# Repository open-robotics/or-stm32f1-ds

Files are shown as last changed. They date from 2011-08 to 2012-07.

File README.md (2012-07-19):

OR-STM32F1-DS
=============

Open Robotics controller based on STM32F103VC chip.

Feauters
--------

* 20 servo control outputs
* 8 RoboGPIO with ADC option
* 8 RoboGPIO with servo option
* Onboard dual channel motor H-dirver
* RoboMD2 for additional external motor driver
* Onboard USB
* Separated I<sup>2</sup>C in RoboBUS and RoboI2C
* 2 quadrature encoder inputs

Connectors
----------

* 20 Servo
* 16 RoboGPIO
* 2 brush motor
* 1 RoboBUS
* 1 RoboMD2
* 1 RoboI2C
* 1 USB

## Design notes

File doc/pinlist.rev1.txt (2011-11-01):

Pinlist

Exported from or-stm32-ds.sch at 01.11.11 23:47

EAGLE Version 5.11.0 Copyright (c) 1988-2010 CadSoft

Part     Pad      Pin        Dir      Net

C1       +        +          Pas      VMD
         -        -          Pas      GND

C2       +        +          Pas      VMD
         -        -          Pas      GND

C3       +        +          Pas      VREG5
         -        -          Pas      GND

C4       +        +          Pas      VREG33
         -        -          Pas      GND

C5       1        1          Pas      GND
         2        2          Pas      N$2

C6       1        1          Pas      GND
         2        2          Pas      N$3

C7       1        1          Pas      +3V3
         2        2          Pas      GND

C8       1        1          Pas      +3V3
         2        2          Pas      GND

C9       1        1          Pas      +3V3
         2        2          Pas      GND

C10      1        1          Pas      +3V3
         2        2          Pas      GND

C11      1        1          Pas      +3V3
         2        2          Pas      GND

C12      1        1          Pas      !NRST
         2        2          Pas      GND

C13      1        1          Pas      VREG33
         2        2          Pas      GND

C14      1        1          Pas      VREG5
         2        2          Pas      GND

DA1      1        GND        In       GND
         2        OUT        Pas      VREG5
         3        IN         In       VS1

DA2      1        GND        In       GND
         2        OUT        Pas      VREG33
         3        IN         In       VS1

DD1      1        PE2        I/O      S04
         2        PE3        I/O      S03
         3        PE4        I/O      S02
         4        PE5        I/O      S01
         5        PE6        I/O      S00
         6        VBAT       I/O               *** unconnected ***
         7        PC13-TAMPER-RTC I/O               *** unconnected ***
         8        PC14-OSC32_IN I/O               *** unconnected ***
         9        PC15-OSC32_OUT I/O               *** unconnected ***
         10       VSS_5      Pas      GND
         11       VDD_5      Pwr      +3V3
         12       OSC_IN     In       N$2
         13       OSC_OUT    Out      N$3
         14       !NRST      In       !NRST
         15       PC0        I/O      AG7
         16       PC1        I/O      AG6
         17       PC2        I/O      AG5
         18       PC3        I/O      AG4
         19       VSSA       I/O      GND
         20       VREF-      I/O      GND
         21       VREF+      I/O      +3V3
         22       VDDA       I/O      +3V3
         23       PA0-WKUP   I/O      AG3
         24       PA1        I/O      AG2
         25       PA2        I/O      AG1
         26       PA3        I/O      AG0
         27       VSS_4      Pas      GND
         28       VDD_4      Pwr      +3V3
         29       PA4        I/O      DAC1
         30       PA5        I/O      DAC2
         31       PA6        I/O      E0F0
         32       PA7        I/O      E0F1
         33       PC4        I/O      M0DIRP
         34       PC5        I/O      M0DIRN
         35       PB0        I/O      M1DIRP
         36       PB1        I/O      M1DIRN
         37       PB2-BOOT1  I/O      BOOT1
         38       PE7        I/O      MDDIR1
         39       PE8        I/O      M0PWMN
         40       PE9        I/O      M0PWMP
         41       PE10       I/O      M1PWMN
         42       PE11       I/O      M1PWMP
         43       PE12       I/O      MDDIR2
         44       PE13       I/O      MDPWM1
         45       PE14       I/O      MDPWM2
         46       PE15       I/O               *** unconnected ***
         47       PB10       I/O      I2C-SCL/TX
         48       PB11       I/O      I2C-SDA/RX
         49       VSS_1      Pas      GND
         50       VDD_1      Pwr      +3V3
         51       PB12       I/O      G0
         52       PB13       I/O      G1
         53       PB14       I/O      G2
         54       PB15       I/O      G3
         55       PD8        I/O      G4
         56       PD9        I/O      G5
         57       PD10       I/O      G6
         58       PD11       I/O      G7
         59       PD12       I/O      E1F0
         60       PD13       I/O      E1F1
         61       PD14       I/O      S10
         62       PD15       I/O      S11
         63       PC6        I/O      S12
         64       PC7        I/O      S13
         65       PC8        I/O      S14
         66       PC9        I/O      S15
         67       PA8        I/O      S16
         68       PA9        I/O      U2TX
         69       PA10       I/O      U2RX
         70       PA11       I/O      USBD-
         71       PA12       I/O      USBD+
         72       PA13       I/O      SWDIO
         73       NC         NC                *** unconnected ***
         74       VSS_2      Pas      GND
         75       VDD_2      Pwr      +3V3
         76       PA14       I/O      SWCLK
         77       PA15       I/O      RBGP0
         78       PC10       I/O      S17
         79       PC11       I/O      S18
         80       PC12       I/O      S19
         81       PD0        I/O      RBGP1
         82       PD1        I/O      RBGP2
         83       PD2        I/O      RBGP0
         84       PD3        I/O               *** unconnected ***
         85       PD4        I/O               *** unconnected ***
         86       PD5        I/O      S09
         87       PD6        I/O      S08
         88       PD7        I/O      S07
         89       PB3        I/O      RBSCK
         90       PB4        I/O      RBMISO
         91       PB5        I/O      RBMOSI
         92       PB6        I/O      RBSCL
         93       PB7        I/O      RBSDA
         94       BOOT0      In       BOOT0
         95       PB8        I/O      CAN_RX
         96       PB9        I/O      CAN_TX
         97       PE0        I/O      S06
         98       PE1        I/O      S05
         99       VSS_3      Pas      GND
         100      VDD_3      Pwr      +3V3

DD2      1        TXD        In       CAN_TX
         2        VSS        Pwr      GND
         3        VDD        Pwr      +3V3
         4        RXD        Out      CAN_RX
         5        VREF       Pwr      VREF
         6        CANL       I/O      CANL
         7        CANH       I/O      CANH
         8        RS         In       CANRS

HL1      A        A          Pas      +3V3
         C        C          Pas      N$6

HL2      A        A          Pas      N$7
         C        C          Pas      GND

HL3      1        C          Pas      N$10
         2        A          Pas      M0C-
         3        C          Pas      M0C-
         4        A          Pas      N$10

HL4      1        C          Pas      N$13
         2        A          Pas      M0C-1
         3        C          Pas      M0C-1
         4        A          Pas      N$13

JP3      1        1          Pas      VREG5
         2        2          Pas      +5V

JP4      1        1          Pas      VREG33
         2        2          Pas      +3V3

JP5      1        1          Pas      U2RX
         2        2          Pas      N$5
         3        3          Pas      N$1
         4        4          Pas      U2TX

JP6      1        1          Pas      +3V3
         2        2          Pas      GPVCC
         3        3          Pas      VS1

JP7      1        1          Pas      +3V3
         2        2          Pas      N$4
         3        3          Pas      VS0

R1       1        1          Pas      GND
         2        2          Pas      N$6

R2       1        1          Pas      +3V3
         2        2          Pas      RBSDA

R3       1        1          Pas      +3V3
         2        2          Pas      RBSCL

R4       1        1          Pas      GND
         2        2          Pas      BOOT1

R5       1        1          Pas      M0DIRP
         2        2          Pas      GND

R6       1        1          Pas      N$7
         2        2          Pas      BOOT1

R7       1        1          Pas      GND
         2        2          Pas      M0PWMP

R8       1        1          Pas      N$8
         2        2          Pas      VMD

R9       1        1          Pas      M0C+
         2        2          Pas      N$10

R10      1        1          Pas      VMD
         2        2          Pas      N$9

R11      1        1          Pas      GND
         2        2          Pas      M0PWMN

R12      1        1          Pas      M0DIRN
         2        2          Pas      GND

R13      1        1          Pas      M1DIRP
         2        2          Pas      GND

R14      1        1          Pas      GND
         2        2          Pas      M1PWMP

R15      1        1          Pas      N$11
         2        2          Pas      VMD

R16      1        1          Pas      BOOT0
         2        2          Pas      GND

R17      1        1          Pas      M0C+1
         2        2          Pas      N$13

R18      1        1          Pas      VMD
         2        2          Pas      N$12

R19      1        1          Pas      GND
         2        2          Pas      M1PWMN

R20      1        1          Pas      I2C-SDA/RX
         2        2          Pas      +5V

R21      1        1          Pas      I2C-SCL/TX
         2        2          Pas      +5V

R22      1        1          Pas      M1DIRN
         2        2          Pas      GND

R23      1        1          Pas      USBD+
         2        2          Pas      +3V3

R24      1        1          Pas      GND
         2        2          Pas      CANRS

R25      1        1          Pas      +5V
         2        2          Pas      S00C

R26      1        1          Pas      +5V
         2        2          Pas      S01C

R27      1        1          Pas      +5V
         2        2          Pas      S02C

R28      1        1          Pas      +5V
         2        2          Pas      S03C

R29      1        1          Pas      +5V
         2        2          Pas      S04C

R30      1        1          Pas      +5V
         2        2          Pas      S05C

R31      1        1          Pas      +5V
         2        2          Pas      S06C

R32      1        1          Pas      +5V
         2        2          Pas      S07C

R33      1        1          Pas      +5V
         2        2          Pas      S08C

R34      1        1          Pas      +5V
         2        2          Pas      S09C

R35      1        1          Pas      +5V
         2        2          Pas      S10C

R36      1        1          Pas      +5V
         2        2          Pas      S11C

R37      1        1          Pas      +5V
         2        2          Pas      S12C

R38      1        1          Pas      +5V
         2        2          Pas      S13C

R39      1        1          Pas      +5V
         2        2          Pas      S14C

R40      1        1          Pas      +5V
         2        2          Pas      S15C

R41      1        1          Pas      +5V
         2        2          Pas      S16C

R42      1        1          Pas      +5V
         2        2          Pas      S17C

R43      1        1          Pas      +5V
         2        2          Pas      S18C

R44      1        1          Pas      +5V
         2        2          Pas      S19C

R45      1        1          Pas      N$5
         2        2          Pas      RBTXD

R46      1        1          Pas      N$1
         2        2          Pas      RBRXD

R47      1        1          Pas      S00
         2        2          Pas      S00C

R48      1        1          Pas      S01
         2        2          Pas      S01C

R49      1        1          Pas      S02
         2        2          Pas      S02C

R50      1        1          Pas      S03
         2        2          Pas      S03C

R51      1        1          Pas      S04
         2        2          Pas      S04C

R52      1        1          Pas      S05
         2        2          Pas      S05C

R53      1        1          Pas      S06
         2        2          Pas      S06C

R54      1        1          Pas      S07
         2        2          Pas      S07C

R55      1        1          Pas      S08
         2        2          Pas      S08C

R56      1        1          Pas      S09
         2        2          Pas      S09C

R57      1        1          Pas      S10
         2        2          Pas      S10C

R58      1        1          Pas      S11
         2        2          Pas      S11C

R59      1        1          Pas      S12
         2        2          Pas      S12C

R60      1        1          Pas      S13
         2        2          Pas      S13C

R61      1        1          Pas      S14
         2        2          Pas      S14C

R62      1        1          Pas      S15
         2        2          Pas      S15C

R63      1        1          Pas      S16
         2        2          Pas      S16C

R64      1        1          Pas      S17
         2        2          Pas      S17C

R65      1        1          Pas      S18
         2        2          Pas      S18C

R66      1        1          Pas      S19
         2        2          Pas      S19C

R67      1        1          Pas      G0
         2        2          Pas      G0C

R68      1        1          Pas      G1
         2        2          Pas      G1C

R69      1        1          Pas      G2
         2        2          Pas      G2C

R70      1        1          Pas      G3
         2        2          Pas      G3C

R71      1        1          Pas      G4
         2        2          Pas      G4C

R72      1        1          Pas      G5
         2        2          Pas      G5C

R73      1        1          Pas      G6
         2        2          Pas      G6C

R74      1        1          Pas      G7
         2        2          Pas      G7C

R75      1        1          Pas      AG0
         2        2          Pas      AG0C

R76      1        1          Pas      AG1
         2        2          Pas      AG1C

R77      1        1          Pas      AG2
         2        2          Pas      AG2C

R78      1        1          Pas      AG3
         2        2          Pas      AG3C

R79      1        1          Pas      AG4
         2        2          Pas      AG4C

R80      1        1          Pas      AG5
         2        2          Pas      AG5C

R81      1        1          Pas      AG6
         2        2          Pas      AG6C

R82      1        1          Pas      AG7
         2        2          Pas      AG7C

SV1      1        1          Pas      GND
         2        2          Pas      GND
         3        3          Pas      !NRST
         4        4          Pas               *** unconnected ***

SV2      1        1          Pas      BOOT0
         2        2          Pas               *** unconnected ***
         3        3          Pas      +3V3
         4        4          Pas               *** unconnected ***

VT1      1        G          Pas      M0DIRP
         2        S          Pas      GND
         3        D          Pas      N$8

VT2      1        S          Pas      GND
         2        G          Pas      M0PWMP
         3        S          Pas      VMD
         4        G          Pas      N$8
         5        D          Pas      M0C+
         6        D2         Pas      M0C+
         7        D          Pas      M0C+
         8        D2         Pas      M0C+

VT3      1        S          Pas      GND
         2        G          Pas      M0PWMN
         3        S          Pas      VMD
         4        G          Pas      N$9
         5        D          Pas      M0C-
         6        D2         Pas      M0C-
         7        D          Pas      M0C-
         8        D2         Pas      M0C-

VT4      1        G          Pas      M0DIRN
         2        S          Pas      GND
         3        D          Pas      N$9

VT5      1        G          Pas      M1DIRP
         2        S          Pas      GND
         3        D          Pas      N$11

VT6      1        S          Pas      GND
         2        G          Pas      M1PWMP
         3        S          Pas      VMD
         4        G          Pas      N$11
         5        D          Pas      M0C+1
         6        D2         Pas      M0C+1
         7        D          Pas      M0C+1
         8        D2         Pas      M0C+1

VT7      1        S          Pas      GND
         2        G          Pas      M1PWMN
         3        S          Pas      VMD
         4        G          Pas      N$12
         5        D          Pas      M0C-1
         6        D2         Pas      M0C-1
         7        D          Pas      M0C-1
         8        D2         Pas      M0C-1

VT8      1        G          Pas      M1DIRN
         2        S          Pas      GND
         3        D          Pas      N$12

X1       1        KL         Pas      VMD
         2        KL         Pas      GND

X2       1        1          Pas      GND
         2        2          Pas      GND
         3        3          Pas      DAC1
         4        4          Pas      DAC2

X3       1        KL         Pas      M0C+
         2        KL         Pas      M0C-

X4       1        KL         Pas      M0C+1
         2        KL         Pas      M0C-1

X5       D+       D+         I/O      USBD+
         D-       D-         I/O      USBD-
         GND      GND        I/O      GND
         VBUS     VBUS       I/O               *** unconnected ***

X6       1        1          Pas      GND
         2        2          Pas      I2C-SCL/TX
         3        3          Pas      I2C-SDA/RX
         4        4          Pas      +5V

X7       1        1          Pas      E0F0
         2        2          Pas      E0F1
         3        3          Pas      +5V
         4        4          Pas      GND

X8       1        1          Pas      E1F0
         2        2          Pas      E1F1
         3        3          Pas      +5V
         4        4          Pas      GND

X9       1        1          Pas      +3V3
         2        2          Pas      SWCLK
         3        3          Pas      GND
         4        4          Pas      SWDIO

X10      1        1          Pas      GND
         2        2          Pas      CANH
         3        3          Pas      CANL
         4        4          Pas      GND

X11      1        GND        Pas      GND
         2        3V3        Pas      +3V3
         3        RESET      Pas               *** unconnected ***
         4        MOSI       Pas      RBMOSI
         5        MISO       Pas      RBMISO
         6        SCK        Pas      RBSCK
         7        GP2        Pas      RBGP2
         8        GP1        Pas      RBGP1
         9        GP0        Pas      RBGP0
         10       SDA        Pas      RBSDA
         11       SCL        Pas      RBSCL
         12       TXD        Pas      RBTXD
         13       RXD        Pas      RBRXD
         14       5V         Pas      +5V

X12      1        1          Pas      S00C
         2        2          Pas      S01C
         3        3          Pas      S02C
         4        4          Pas      S03C
         5        5          Pas      S04C
         6        6          Pas      S05C
         7        7          Pas      S06C
         8        8          Pas      S07C
         9        9          Pas      S08C
         10       10         Pas      S09C

X13      1        1          Pas      S10C
         2        2          Pas      S11C
         3        3          Pas      S12C
         4        4          Pas      S13C
         5        5          Pas      S14C
         6        6          Pas      S15C
         7        7          Pas      S16C
         8        8          Pas      S17C
         9        9          Pas      S18C
         10       10         Pas      S19C

X14      1        1          Pas      G0C
         2        2          Pas      G1C
         3        3          Pas      G2C
         4        4          Pas      G3C
         5        5          Pas      G4C
         6        6          Pas      G5C
         7        7          Pas      G6C
         8        8          Pas      G7C

X15      1        1          Pas      AG0C
         2        2          Pas      AG1C
         3        3          Pas      AG2C
         4        4          Pas      AG3C
         5        5          Pas      AG4C
         6        6          Pas      AG5C
         7        7          Pas      AG6C
         8        8          Pas      AG7C

X16      1        PWM2       Pas      MDPWM2
         2        PWM1       Pas      MDPWM1
         3        OVLD2      Pas               *** unconnected ***
         4        OVLD1      Pas               *** unconnected ***
         5        DIR2       Pas      MDDIR2
         6        DIR1       Pas      MDDIR1
         7        SENS2      Pas               *** unconnected ***
         8        SENS1      Pas               *** unconnected ***
         9        VSS1       Pas               *** unconnected ***
         10       GND1       Pas      GND
         11       VSS2       Pas               *** unconnected ***
         12       GND2       Pas      GND

X17      1        1          Pas      VS0
         2        2          Pas      VS0
         3        3          Pas      VS0
         4        4          Pas      VS0
         5        5          Pas      VS0
         6        6          Pas      VS0
         7        7          Pas      VS0
         8        8          Pas      VS0
         9        9          Pas      VS0
         10       10         Pas      VS0

X18      1        1          Pas      VS1
         2        2          Pas      VS1
         3        3          Pas      VS1
         4        4          Pas      VS1
         5        5          Pas      VS1
         6        6          Pas      VS1
         7        7          Pas      VS1
         8        8          Pas      VS1
         9        9          Pas      VS1
         10       10         Pas      VS1

X19      1        1          Pas      GPVCC
         2        2          Pas      GPVCC
         3        3          Pas      GPVCC
         4        4          Pas      GPVCC
         5        5          Pas      GPVCC
         6        6          Pas      GPVCC
         7        7          Pas      GPVCC
         8        8          Pas      GPVCC

X20      1        1          Pas      N$4
         2        2          Pas      N$4
         3        3          Pas      N$4
         4        4          Pas      N$4
         5        5          Pas      N$4
         6        6          Pas      N$4
         7        7          Pas      N$4
         8        8          Pas      N$4

X21      1        1          Pas      GND
         2        2          Pas      GND
         3        3          Pas      GND
         4        4          Pas      GND
         5        5          Pas      GND
         6        6          Pas      GND
         7        7          Pas      GND
         8        8          Pas      GND
         9        9          Pas      GND
         10       10         Pas      GND

X22      1        1          Pas      GND
         2        2          Pas      GND
         3        3          Pas      GND
         4        4          Pas      GND
         5        5          Pas      GND
         6        6          Pas      GND
         7        7          Pas      GND
         8        8          Pas      GND
         9        9          Pas      GND
         10       10         Pas      GND

X23      1        1          Pas      GND
         2        2          Pas      GND
         3        3          Pas      GND
         4        4          Pas      GND
         5        5          Pas      GND
         6        6          Pas      GND
         7        7          Pas      GND
         8        8          Pas      GND

X24      1        1          Pas      GND
         2        2          Pas      GND
         3        3          Pas      GND
         4        4          Pas      GND
         5        5          Pas      GND
         6        6          Pas      GND
         7        7          Pas      GND
         8        8          Pas      GND

X25      1        KL         Pas      VS0
         2        KL         Pas      GND

X26      1        KL         Pas      VS1
         2        KL         Pas      GND

X27      1        1          Pas      +5V
         2        2          Pas      +5V
         3        3          Pas      +5V
         4        4          Pas      +5V
         5        5          Pas      +5V
         6        6          Pas      +5V
         7        7          Pas      +5V
         8        8          Pas      +5V

X28      1        1          Pas      +5V
         2        2          Pas      +5V
         3        3          Pas      +5V
         4        4          Pas      +5V
         5        5          Pas      +5V
         6        6          Pas      +5V
         7        7          Pas      +5V
         8        8          Pas      +5V

ZQ1      1        1          Pas      N$3
         2        2          Pas      N$2

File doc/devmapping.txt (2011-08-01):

# vim:set ft=yaml

TIM1:
  mode: PWM
  CH1:  M0PWMP
  CH1N: M0PWMN
  CH2:  M1PWMP
  CH2N: M1PWMN
  CH3:  MDPWM1
  CH4:  MDPWM2

TIM3:
  mode: Encoder
  CH1:  E0F0
  CH2:  E0F1

TIM4:
  mode: Encoder
  CH1:  E1F0
  CH2:  E1F1

USB:
  D+: USBD+
  D-: USBD-

USART1:
  RX: RBRX
  TX: RBTX

I2C1:
  SDA: RBSDA
  SCL: RBSCL

SPI3:
  MISO: RBMISO
  MOSI: RBMOSI
  SCK:  RBSCK
  NSS:  RBGP0

remap_xor:
  I2C2:
    SDA: I2C-SDA/RX
    SCL: I2C-SCL/TX
  USART3:
    RX: I2C-SDA/RX
    TX: I2C-SDA/TX

CAN1:
  remapped: true
  RX: CAN_RX
  TX: CAN_TX

SWD:
  SWCLK: SWCLK
  SWDIO: SWDIO

ADC:
  IN10: AG7
  IN11: AG6
  IN12: AG5
  IN13: AG4
  IN0:  AG3
  IN1:  AG2
  IN2:  AG1
  IN3:  AG0

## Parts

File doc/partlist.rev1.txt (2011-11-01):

Partlist

Exported from or-stm32-ds.sch at 01.11.11 23:47

EAGLE Version 5.11.0 Copyright (c) 1988-2010 CadSoft

Part     Value          Device          Package            Library                 Sheet

C1       100uF 16V      CPOL-EUE3.5-8   E3,5-8             rcl                     1
C2       100uF 16V      CPOL-EUE3.5-8   E3,5-8             rcl                     1
C3       100uF 16V      CPOL-EUE3.5-8   E3,5-8             rcl                     1
C4       100uF 16V      CPOL-EUE3.5-8   E3,5-8             rcl                     1
C5       22p            C-EUC0603       C0603              rcl                     1
C6       22p            C-EUC0603       C0603              rcl                     1
C7       0.1            C-EUC0603       C0603              rcl                     1
C8       0.1            C-EUC0603       C0603              rcl                     1
C9       0.1            C-EUC0603       C0603              rcl                     1
C10      0.1            C-EUC0603       C0603              rcl                     1
C11      0.1            C-EUC0603       C0603              rcl                     1
C12      0.022          C-EUC0603       C0603              rcl                     1
C13      0.1            C-EUC0603       C0603              rcl                     1
C14      0.1            C-EUC0603       C0603              rcl                     1
DA1      5V             LM1117          SOT223             v-reg-3                 1
DA2      3.3V           LM1117          SOT223             v-reg-3                 1
DD1      STM32F103VC    STM32F103VC     LQFP100            stm32f103               1
DD2      MCP2551SN      MCP2551SN       SO-08              can                     1
HL1                     LEDCHIP-LED0805 CHIP-LED0805       led                     1
HL2                     LEDCHIP-LED0805 CHIP-LED0805       led                     1
HL3      KAA-3528ESGC   KAA-3528ESGC    KA-3528            led2                    1
HL4      KAA-3528ESGC   KAA-3528ESGC    KA-3528            led2                    1
JP3                     JP1E            JP1                con-std                 1
JP4                     JP1E            JP1                con-std                 1
JP5                     JP2Q            JP2Q               jumper                  1
JP6                     JP2E            JP2                con-std                 1
JP7                     JP2E            JP2                con-std                 1
R1       250            R-EU_R0603      R0603              rcl                     1
R2       4.7k           R-EU_R0603      R0603              rcl                     1
R3       4.7k           R-EU_R0603      R0603              rcl                     1
R4       10k            R-EU_R0603      R0603              rcl                     1
R5       5.1k           R-EU_R0603      R0603              rcl                     1
R6       250            R-EU_R0603      R0603              rcl                     1
R7       5.1k           R-EU_R0603      R0603              rcl                     1
R8       1k             R-EU_R0603      R0603              rcl                     1
R9       820            R-EU_R0603      R0603              rcl                     1
R10      1k             R-EU_R0603      R0603              rcl                     1
R11      5.1k           R-EU_R0603      R0603              rcl                     1
R12      5.1k           R-EU_R0603      R0603              rcl                     1
R13      5.1k           R-EU_R0603      R0603              rcl                     1
R14      5.1k           R-EU_R0603      R0603              rcl                     1
R15      1k             R-EU_R0603      R0603              rcl                     1
R16      10k            R-EU_R0603      R0603              rcl                     1
R17      820            R-EU_R0603      R0603              rcl                     1
R18      1k             R-EU_R0603      R0603              rcl                     1
R19      5.1k           R-EU_R0603      R0603              rcl                     1
R20      4.7k           R-EU_R0603      R0603              rcl                     1
R21      4.7k           R-EU_R0603      R0603              rcl                     1
R22      5.1k           R-EU_R0603      R0603              rcl                     1
R23      1.5k           R-EU_R0603      R0603              rcl                     1
R24      10k            R-EU_R0603      R0603              rcl                     1
R25      4.7k           R-EU_R0603      R0603              rcl                     1
R26      4.7k           R-EU_R0603      R0603              rcl                     1
R27      4.7k           R-EU_R0603      R0603              rcl                     1
R28      4.7k           R-EU_R0603      R0603              rcl                     1
R29      4.7k           R-EU_R0603      R0603              rcl                     1
R30      4.7k           R-EU_R0603      R0603              rcl                     1
R31      4.7k           R-EU_R0603      R0603              rcl                     1
R32      4.7k           R-EU_R0603      R0603              rcl                     1
R33      4.7k           R-EU_R0603      R0603              rcl                     1
R34      4.7k           R-EU_R0603      R0603              rcl                     1
R35      4.7k           R-EU_R0603      R0603              rcl                     1
R36      4.7k           R-EU_R0603      R0603              rcl                     1
R37      4.7k           R-EU_R0603      R0603              rcl                     1
R38      4.7k           R-EU_R0603      R0603              rcl                     1
R39      4.7k           R-EU_R0603      R0603              rcl                     1
R40      4.7k           R-EU_R0603      R0603              rcl                     1
R41      4.7k           R-EU_R0603      R0603              rcl                     1
R42      4.7k           R-EU_R0603      R0603              rcl                     1
R43      4.7k           R-EU_R0603      R0603              rcl                     1
R44      4.7k           R-EU_R0603      R0603              rcl                     1
R45      150            R-EU_R0603      R0603              rcl                     1
R46      150            R-EU_R0603      R0603              rcl                     1
R47      150            R-EU_R0603      R0603              rcl                     1
R48      150            R-EU_R0603      R0603              rcl                     1
R49      150            R-EU_R0603      R0603              rcl                     1
R50      150            R-EU_R0603      R0603              rcl                     1
R51      150            R-EU_R0603      R0603              rcl                     1
R52      150            R-EU_R0603      R0603              rcl                     1
R53      150            R-EU_R0603      R0603              rcl                     1
R54      150            R-EU_R0603      R0603              rcl                     1
R55      150            R-EU_R0603      R0603              rcl                     1
R56      150            R-EU_R0603      R0603              rcl                     1
R57      150            R-EU_R0603      R0603              rcl                     1
R58      150            R-EU_R0603      R0603              rcl                     1
R59      150            R-EU_R0603      R0603              rcl                     1
R60      150            R-EU_R0603      R0603              rcl                     1
R61      150            R-EU_R0603      R0603              rcl                     1
R62      150            R-EU_R0603      R0603              rcl                     1
R63      150            R-EU_R0603      R0603              rcl                     1
R64      150            R-EU_R0603      R0603              rcl                     1
R65      150            R-EU_R0603      R0603              rcl                     1
R66      150            R-EU_R0603      R0603              rcl                     1
R67      150            R-EU_R0603      R0603              rcl                     1
R68      150            R-EU_R0603      R0603              rcl                     1
R69      150            R-EU_R0603      R0603              rcl                     1
R70      150            R-EU_R0603      R0603              rcl                     1
R71      150            R-EU_R0603      R0603              rcl                     1
R72      150            R-EU_R0603      R0603              rcl                     1
R73      150            R-EU_R0603      R0603              rcl                     1
R74      150            R-EU_R0603      R0603              rcl                     1
R75      150            R-EU_R0603      R0603              rcl                     1
R76      150            R-EU_R0603      R0603              rcl                     1
R77      150            R-EU_R0603      R0603              rcl                     1
R78      150            R-EU_R0603      R0603              rcl                     1
R79      150            R-EU_R0603      R0603              rcl                     1
R80      150            R-EU_R0603      R0603              rcl                     1
R81      150            R-EU_R0603      R0603              rcl                     1
R82      150            R-EU_R0603      R0603              rcl                     1
SV1                     TAC_SWITCHSMD   TACTILE_SWITCH_SMD SparkFun                1
SV2                     TAC_SWITCHSMD   TACTILE_SWITCH_SMD SparkFun                1
VT1      BSS123         BSS123          SOT23              transistor-small-signal 1
VT2                     PN_MOSFET-SO8   SO8                zetex                   1
VT3                     PN_MOSFET-SO8   SO8                zetex                   1
VT4      BSS123         BSS123          SOT23              transistor-small-signal 1
VT5      BSS123         BSS123          SOT23              transistor-small-signal 1
VT6                     PN_MOSFET-SO8   SO8                zetex                   1
VT7                     PN_MOSFET-SO8   SO8                zetex                   1
VT8      BSS123         BSS123          SOT23              transistor-small-signal 1
X1                      HT396R-02P      HT396R-02P         con-std                 1
X2                      MA04-11.27MM    1X04-1.27MM        con-std                 1
X3                      HT396R-02P      HT396R-02P         con-std                 1
X4                      HT396R-02P      HT396R-02P         con-std                 1
X5       USBSMD         USBSMD          USB-MINIB          SparkFun                1
X6                      MA04-1          MA04-1             con-std                 1
X7                      MA04-1          MA04-1             con-std                 1
X8                      MA04-1          MA04-1             con-std                 1
X9                      MA04-11.27MM    1X04-1.27MM        con-std                 1
X10                     MA04-1          MA04-1             con-std                 1
X11                     ROBOBUSR        ML14L              robobus                 1
X12                     MA10-1          MA10-1             con-std                 1
X13                     MA10-1          MA10-1             con-std                 1
X14                     MA08-1          MA08-1             con-std                 1
X15                     MA08-1          MA08-1             con-std                 1
X16      ROBOMD2        ROBOMD2         ML12               robobus                 1
X17                     MA10-1          MA10-1             con-std                 1
X18                     MA10-1          MA10-1             con-std                 1
X19                     MA08-1          MA08-1             con-std                 1
X20                     MA08-1          MA08-1             con-std                 1
X21                     MA10-1          MA10-1             con-std                 1
X22                     MA10-1          MA10-1             con-std                 1
X23                     MA08-1          MA08-1             con-std                 1
X24                     MA08-1          MA08-1             con-std                 1
X25                     W237-02P        W237-132           con-std                 1
X26                     W237-02P        W237-132           con-std                 1
X27                     MA08-1          MA08-1             con-std                 1
X28                     MA08-1          MA08-1             con-std                 1
ZQ1      8MHz           CRYSTALHC49U-V  HC49U-V            crystal                 1

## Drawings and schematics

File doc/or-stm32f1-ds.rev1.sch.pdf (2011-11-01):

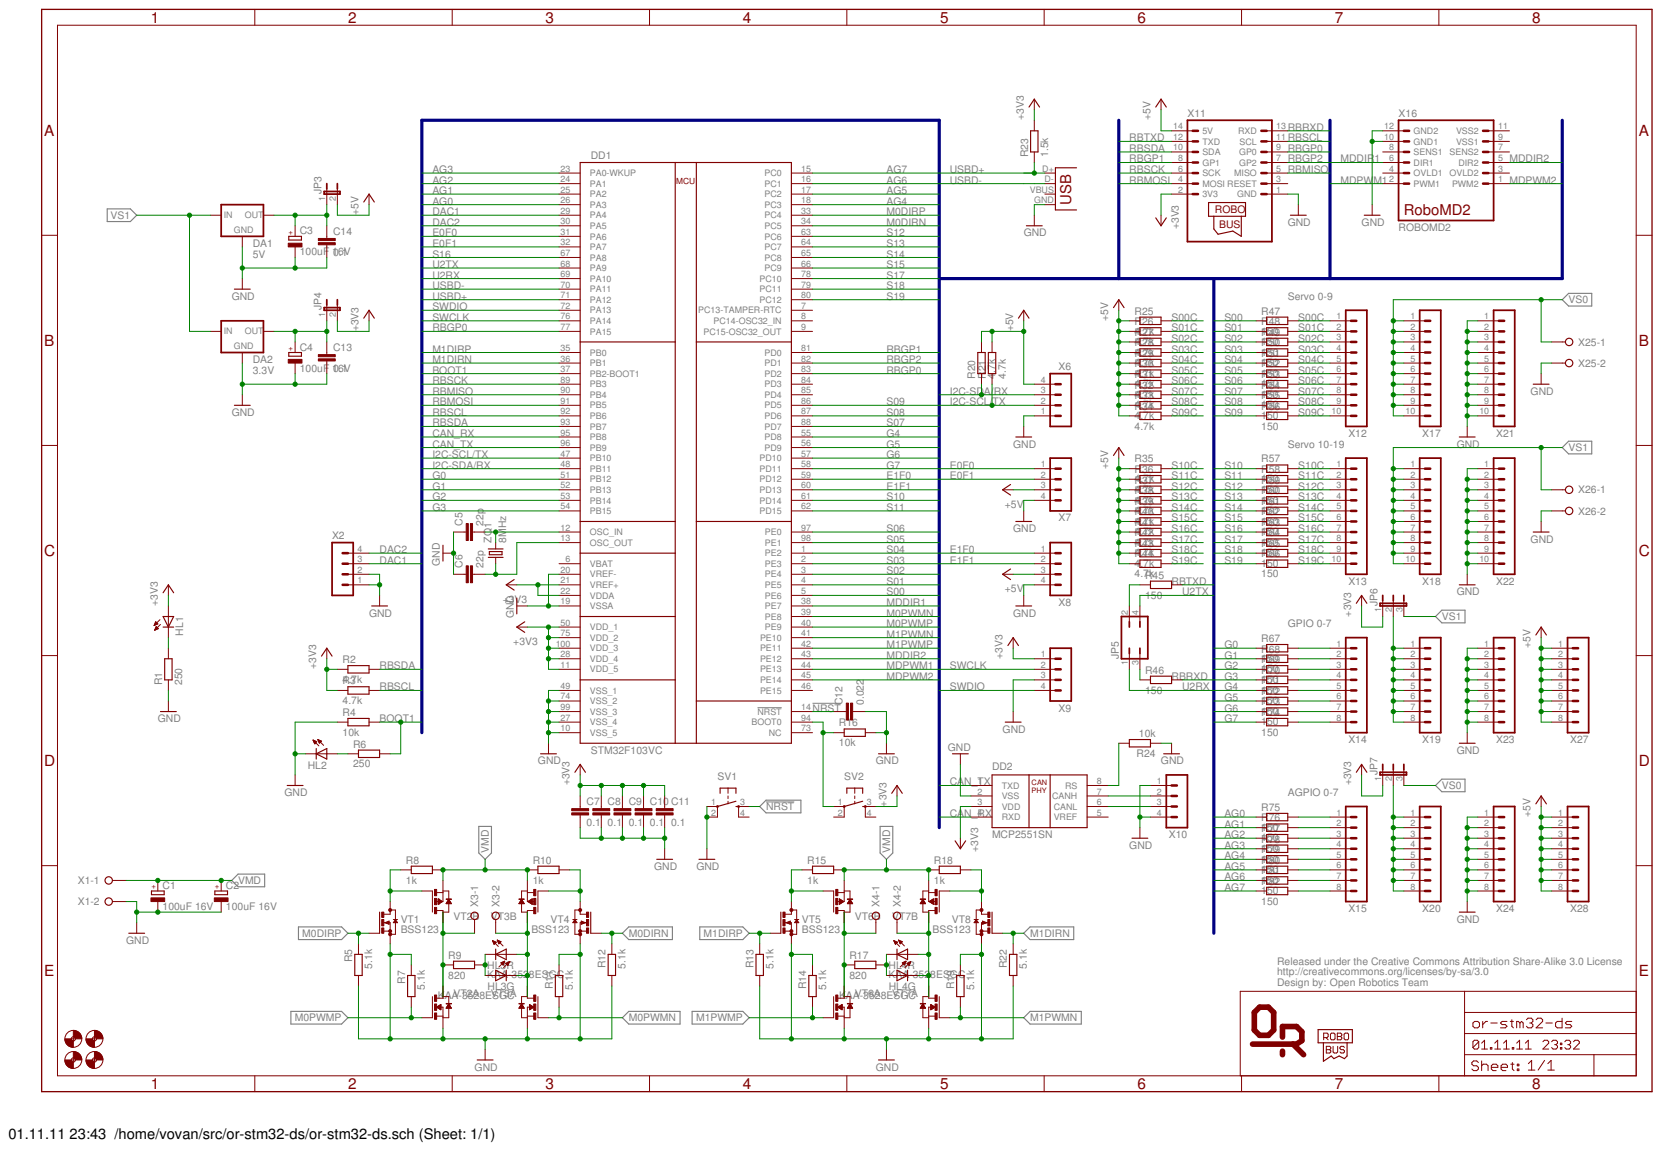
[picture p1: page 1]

Released under the Creative Commons Attribution Share-Alike 3.0 License
http://creativecommons.org/licenses/by-sa/3.0
Design by: Open Robotics Team

01.11.11 23:43 /home/vovan/src/or-stm32-ds/or-stm32-ds.sch (Sheet: 1/1)

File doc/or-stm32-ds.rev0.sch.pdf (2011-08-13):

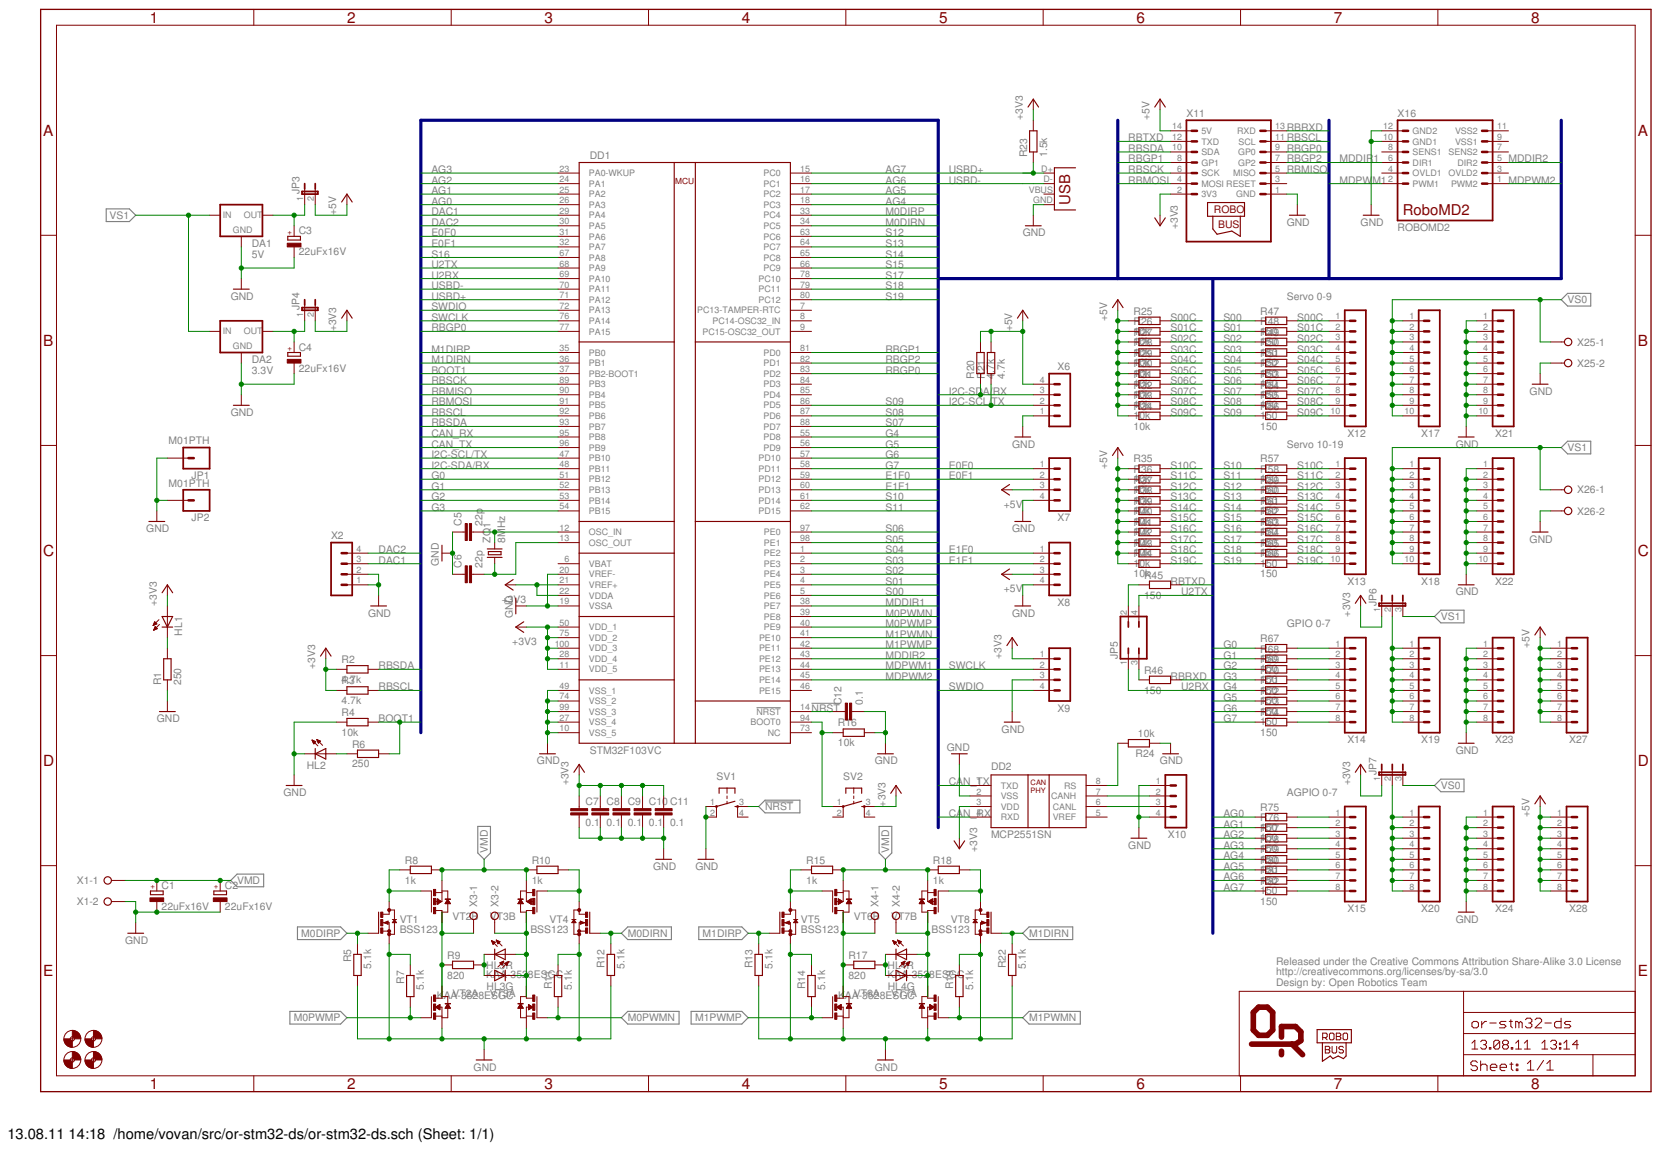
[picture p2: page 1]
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

13.08.11 14:18 /home/vovan/src/or-stm32-ds/or-stm32-ds.sch (Sheet: 1/1)

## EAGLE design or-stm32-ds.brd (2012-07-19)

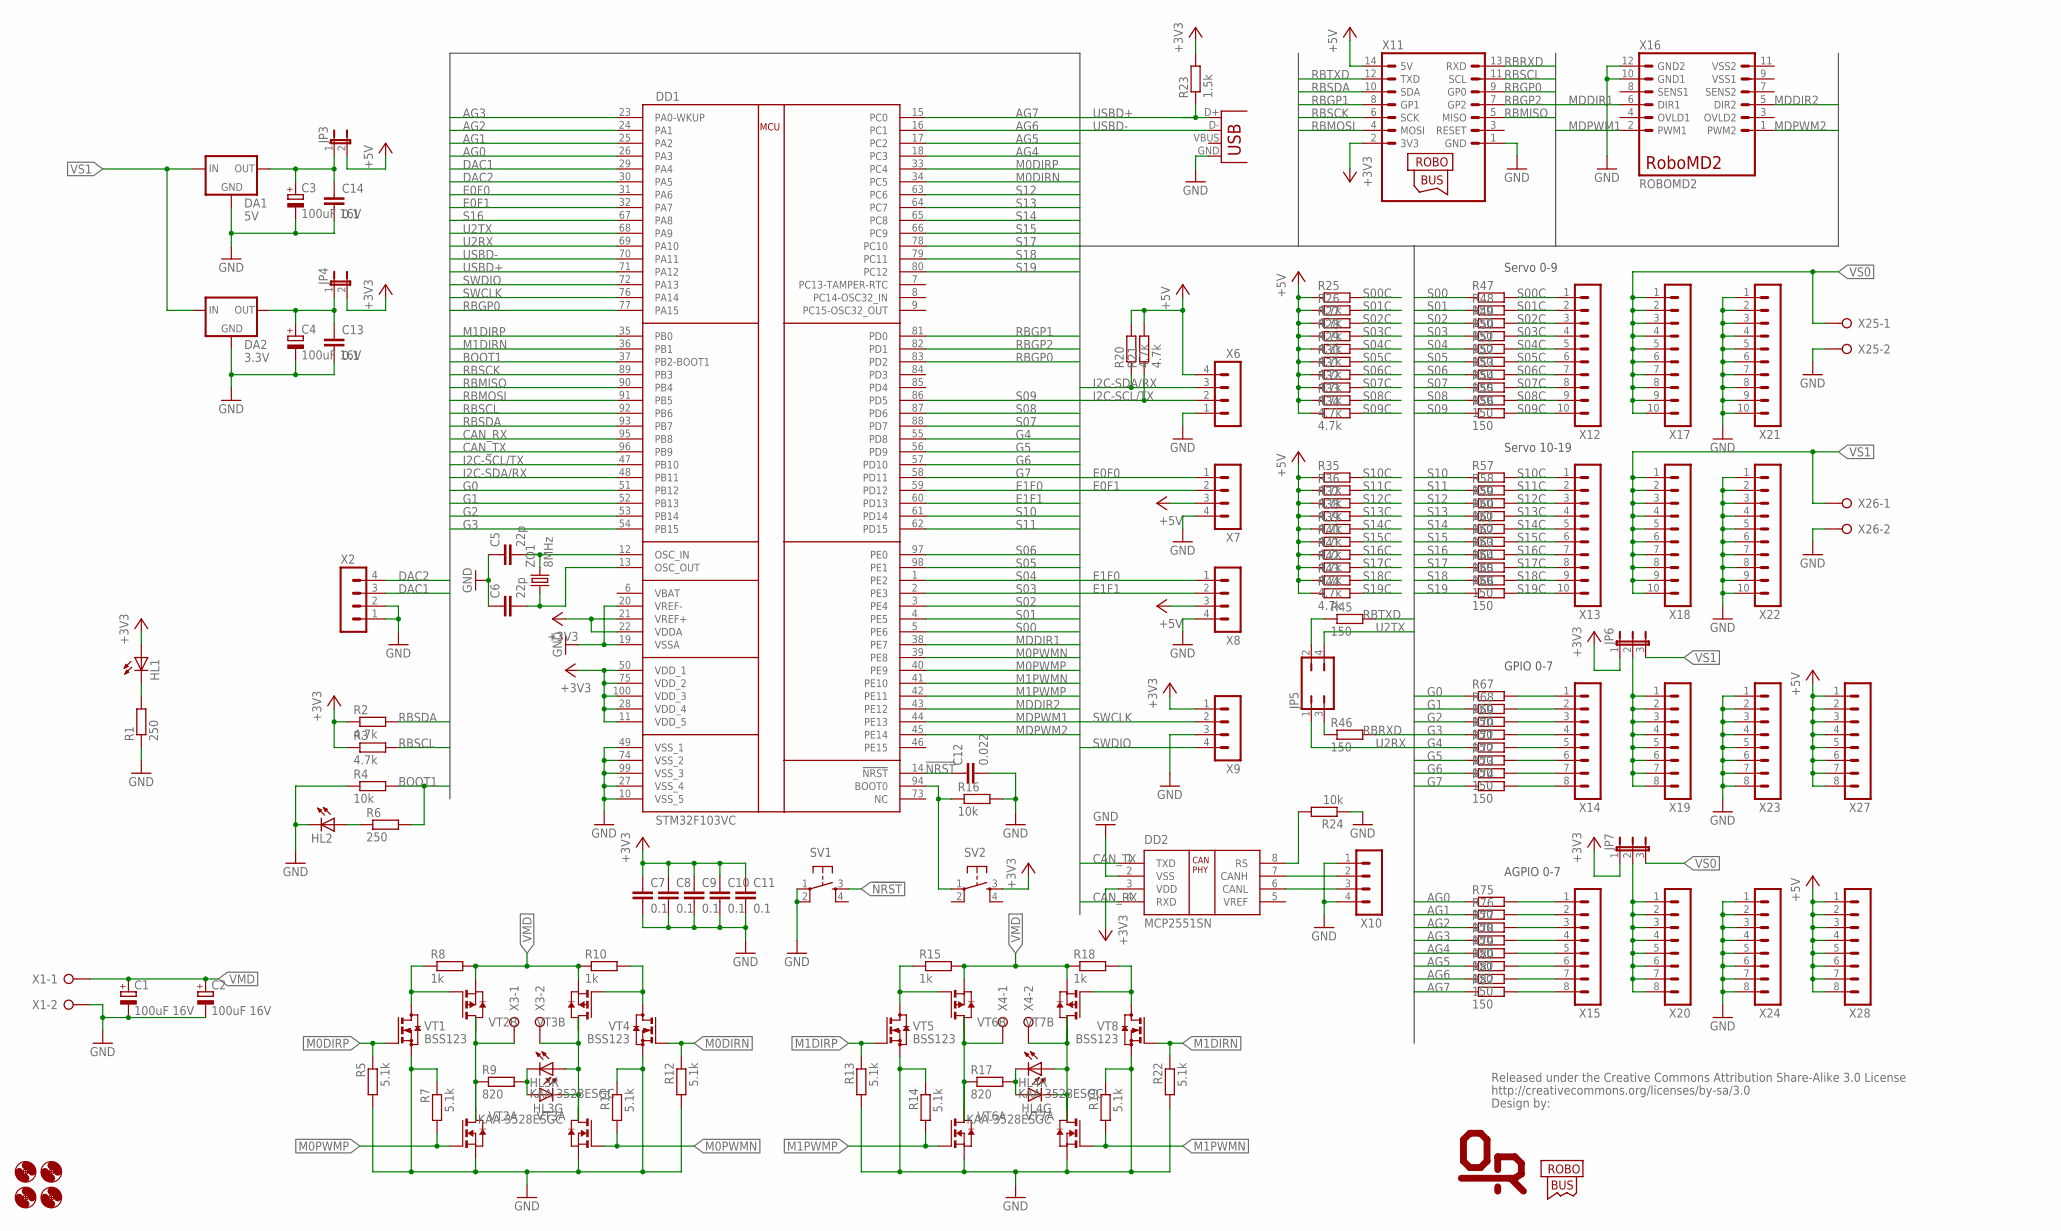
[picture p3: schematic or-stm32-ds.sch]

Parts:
C1, C2, C3, C4: 100uF 16V; E3,5-8
C5, C6: 22p; C0603
C7, C8, C9, C10, C11, C13, C14: 0.1; C0603
C12: 0.022; C0603
DA1: 5V; SOT223
DA2: 3.3V; SOT223
DD1: STM32F103VC; LQFP100
DD2: MCP2551SN; SO-08
H1, H2, H3, H4: MOUNT-HOLE3.2; 3,2
HL1, HL2: LEDCHIP-LED0805; CHIP-LED0805
HL3, HL4: KAA-3528ESGC; KA-3528
JP3, JP4: JP1E; JP1
JP5: JP2Q
JP6, JP7: JP2E; JP2
R1, R6: 250; R0603
R2, R3, R20, R21, R25, R26, R27, R28, R29, R30, R31, R32, R33, R34, R35, R36, R37, R38, R39, R40, R41, R42, R43, R44: 4.7k; R0603
R4, R16, R24: 10k; R0603
R5, R7, R11, R12, R13, R14, R19, R22: 5.1k; R0603
R8, R10, R15, R18: 1k; R0603
R9, R17: 820; R0603
R23: 1.5k; R0603
R45, R46, R47, R48, R49, R50, R51, R52, R53, R54, R55, R56, R57, R58, R59, R60, R61, R62, R63, R64, R65, R66, R67, R68, R69, R70, R71, R72, R73, R74, R75, R76, R77, R78, R79, R80, R81, R82: 150; R0603
SV1, SV2: TAC_SWITCHSMD; TACTILE_SWITCH_SMD
U$1: CREATIVE_COMMONS_BY-SA; CC-BY-SA-6MM
U$2: ORLOGO
U$3: ROBOBUS_LOGO
VT1, VT4, VT5, VT8: BSS123; SOT23
VT2, VT3, VT6, VT7: PN_MOSFET-SO8; SO8
X1, X3, X4: HT396R-02P
X2, X9: MA04-11.27MM; 1X04-1.27MM
X5: USBSMD; USB-MINIB
X6, X7, X8, X10: MA04-1
X11: ROBOBUSR; ML14L
X12, X13, X17, X18, X21, X22: MA10-1
X14, X15, X19, X20, X23, X24, X27, X28: MA08-1
X16: ROBOMD2; ML12
X25, X26: W237-02P; W237-132
ZQ1: 8MHz; HC49U-V

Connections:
!NRST: C12.1, DD1.14 (!NRST), SV1.3
+3V3: C7.1, C8.1, C9.1, C10.1, C11.1, DD1.11 (VDD_5), DD1.21 (VREF+), DD1.22 (VDDA), DD1.28 (VDD_4), DD1.50 (VDD_1), DD1.75 (VDD_2), DD1.100 (VDD_3), DD2.3 (VDD), HL1.A, JP4.2, JP6.1, JP7.1, R2.1, R3.1, R23.2, SV2.3, X9.1, X11.2 (3V3)
+5V: JP3.2, R20.2, R21.2, R25.1, R26.1, R27.1, R28.1, R29.1, R30.1, R31.1, R32.1, R33.1, R34.1, R35.1, R36.1, R37.1, R38.1, R39.1, R40.1, R41.1, R42.1, R43.1, R44.1, X6.4, X7.3, X8.3, X11.14 (5V), X27.1, X27.2, X27.3, X27.4, X27.5, X27.6, X27.7, X27.8, X28.1, X28.2, X28.3, X28.4, X28.5, X28.6, X28.7, X28.8
AG0: DD1.26 (PA3), R75.1
AG0C: R75.2, X15.1
AG1: DD1.25 (PA2), R76.1
AG1C: R76.2, X15.2
AG2: DD1.24 (PA1), R77.1
AG2C: R77.2, X15.3
AG3: DD1.23 (PA0-WKUP), R78.1
AG3C: R78.2, X15.4
AG4: DD1.18 (PC3), R79.1
AG4C: R79.2, X15.5
AG5: DD1.17 (PC2), R80.1
AG5C: R80.2, X15.6
AG6: DD1.16 (PC1), R81.1
AG6C: R81.2, X15.7
AG7: DD1.15 (PC0), R82.1
AG7C: R82.2, X15.8
BOOT0: DD1.94 (BOOT0), R16.1, SV2.1
BOOT1: DD1.37 (PB2-BOOT1), R4.2, R6.2
CANH: DD2.7 (CANH), X10.2
CANL: DD2.6 (CANL), X10.3
CANRS: DD2.8 (RS), R24.2
CAN_RX: DD1.95 (PB8), DD2.4 (RXD)
CAN_TX: DD1.96 (PB9), DD2.1 (TXD)
DAC1: DD1.29 (PA4), X2.3
DAC2: DD1.30 (PA5), X2.4
E0F0: DD1.31 (PA6), X7.1
E0F1: DD1.32 (PA7), X7.2
E1F0: DD1.59 (PD12), X8.1
E1F1: DD1.60 (PD13), X8.2
G0: DD1.51 (PB12), R67.1
G0C: R67.2, X14.1
G1: DD1.52 (PB13), R68.1
G1C: R68.2, X14.2
G2: DD1.53 (PB14), R69.1
G2C: R69.2, X14.3
G3: DD1.54 (PB15), R70.1
G3C: R70.2, X14.4
G4: DD1.55 (PD8), R71.1
G4C: R71.2, X14.5
G5: DD1.56 (PD9), R72.1
G5C: R72.2, X14.6
G6: DD1.57 (PD10), R73.1
G6C: R73.2, X14.7
G7: DD1.58 (PD11), R74.1
G7C: R74.2, X14.8
GND: C1.-, C2.-, C3.-, C4.-, C5.1, C6.1, C7.2, C8.2, C9.2, C10.2, C11.2, C12.2, C13.2, C14.2, DA1.1 (GND), DA2.1 (GND), DD1.10 (VSS_5), DD1.19 (VSSA), DD1.20 (VREF-), DD1.27 (VSS_4), DD1.49 (VSS_1), DD1.74 (VSS_2), DD1.99 (VSS_3), DD2.2 (VSS), HL2.C, R1.1, R4.1, R5.2, R7.1, R11.1, R12.2, R13.2, R14.1, R16.2, R19.1, R22.2, R24.1, SV1.1, SV1.2, VT1.2 (S), VT2.1 (S), VT3.1 (S), VT4.2 (S), VT5.2 (S), VT6.1 (S), VT7.1 (S), VT8.2 (S), X1.2, X2.1, X2.2, X5.GND, X6.1, X7.4, X8.4, X9.3, X10.1, X10.4, X11.1 (GND), X16.10 (GND1), X16.12 (GND2), X21.1, X21.2, X21.3, X21.4, X21.5, X21.6, X21.7, X21.8, X21.9, X21.10, X22.1, X22.2, X22.3, X22.4, X22.5, X22.6, X22.7, X22.8, X22.9, X22.10, X23.1, X23.2, X23.3, X23.4, X23.5, X23.6, X23.7, X23.8, X24.1, X24.2, X24.3, X24.4, X24.5, X24.6, X24.7, X24.8, X25.2, X26.2
GPVCC: JP6.2, X19.1, X19.2, X19.3, X19.4, X19.5, X19.6, X19.7, X19.8
I2C-SCL/TX: DD1.47 (PB10), R21.1, X6.2
I2C-SDA/RX: DD1.48 (PB11), R20.1, X6.3
M0C+: R9.1, VT2.5 (D), VT2.6 (D2), VT2.7 (D), VT2.8 (D2), X3.1
M0C+1: R17.1, VT6.5 (D), VT6.6 (D2), VT6.7 (D), VT6.8 (D2), X4.1
M0C-: HL3.2 (A), HL3.3 (C), VT3.5 (D), VT3.6 (D2), VT3.7 (D), VT3.8 (D2), X3.2
M0C-1: HL4.2 (A), HL4.3 (C), VT7.5 (D), VT7.6 (D2), VT7.7 (D), VT7.8 (D2), X4.2
M0DIRN: DD1.34 (PC5), R12.1, VT4.1 (G)
M0DIRP: DD1.33 (PC4), R5.1, VT1.1 (G)
M0PWMN: DD1.39 (PE8), R11.2, VT3.2 (G)
M0PWMP: DD1.40 (PE9), R7.2, VT2.2 (G)
M1DIRN: DD1.36 (PB1), R22.1, VT8.1 (G)
M1DIRP: DD1.35 (PB0), R13.1, VT5.1 (G)
M1PWMN: DD1.41 (PE10), R19.2, VT7.2 (G)
M1PWMP: DD1.42 (PE11), R14.2, VT6.2 (G)
MDDIR1: DD1.38 (PE7), X16.6 (DIR1)
MDDIR2: DD1.43 (PE12), X16.5 (DIR2)
MDPWM1: DD1.44 (PE13), X16.2 (PWM1)
MDPWM2: DD1.45 (PE14), X16.1 (PWM2)
unnamed: JP5.3, R46.1
unnamed: C5.2, DD1.12 (OSC_IN), ZQ1.2
unnamed: C6.2, DD1.13 (OSC_OUT), ZQ1.1
unnamed: JP7.2, X20.1, X20.2, X20.3, X20.4, X20.5, X20.6, X20.7, X20.8
unnamed: JP5.2, R45.1
unnamed: HL1.C, R1.2
unnamed: HL2.A, R6.1
unnamed: R8.1, VT1.3 (D), VT2.4 (G)
unnamed: R10.2, VT3.4 (G), VT4.3 (D)
unnamed: HL3.1 (C), HL3.4 (A), R9.2
unnamed: R15.1, VT5.3 (D), VT6.4 (G)
unnamed: R18.2, VT7.4 (G), VT8.3 (D)
unnamed: HL4.1 (C), HL4.4 (A), R17.2
RBGP0: DD1.77 (PA15), DD1.83 (PD2), X11.9 (GP0)
RBGP1: DD1.81 (PD0), X11.8 (GP1)
RBGP2: DD1.82 (PD1), X11.7 (GP2)
RBMISO: DD1.90 (PB4), X11.5 (MISO)
RBMOSI: DD1.91 (PB5), X11.4 (MOSI)
RBRXD: R46.2, X11.13 (RXD)
RBSCK: DD1.89 (PB3), X11.6 (SCK)
RBSCL: DD1.92 (PB6), R3.2, X11.11 (SCL)
RBSDA: DD1.93 (PB7), R2.2, X11.10 (SDA)
RBTXD: R45.2, X11.12 (TXD)
S00: DD1.5 (PE6), R47.1
S00C: R25.2, R47.2, X12.1
S01: DD1.4 (PE5), R48.1
S01C: R26.2, R48.2, X12.2
S02: DD1.3 (PE4), R49.1
S02C: R27.2, R49.2, X12.3
S03: DD1.2 (PE3), R50.1
S03C: R28.2, R50.2, X12.4
S04: DD1.1 (PE2), R51.1
S04C: R29.2, R51.2, X12.5
S05: DD1.98 (PE1), R52.1
S05C: R30.2, R52.2, X12.6
S06: DD1.97 (PE0), R53.1
S06C: R31.2, R53.2, X12.7
S07: DD1.88 (PD7), R54.1
S07C: R32.2, R54.2, X12.8
S08: DD1.87 (PD6), R55.1
S08C: R33.2, R55.2, X12.9
S09: DD1.86 (PD5), R56.1
S09C: R34.2, R56.2, X12.10
S10: DD1.61 (PD14), R57.1
S10C: R35.2, R57.2, X13.1
S11: DD1.62 (PD15), R58.1
S11C: R36.2, R58.2, X13.2
S12: DD1.63 (PC6), R59.1
S12C: R37.2, R59.2, X13.3
S13: DD1.64 (PC7), R60.1
S13C: R38.2, R60.2, X13.4
S14: DD1.65 (PC8), R61.1
S14C: R39.2, R61.2, X13.5
S15: DD1.66 (PC9), R62.1
S15C: R40.2, R62.2, X13.6
S16: DD1.67 (PA8), R63.1
S16C: R41.2, R63.2, X13.7
S17: DD1.78 (PC10), R64.1
S17C: R42.2, R64.2, X13.8
S18: DD1.79 (PC11), R65.1
S18C: R43.2, R65.2, X13.9
S19: DD1.80 (PC12), R66.1
S19C: R44.2, R66.2, X13.10
SWCLK: DD1.76 (PA14), X9.2
SWDIO: DD1.72 (PA13), X9.4
U2RX: DD1.69 (PA10), JP5.1
U2TX: DD1.68 (PA9), JP5.4
USBD+: DD1.71 (PA12), R23.1, X5.D+
USBD-: DD1.70 (PA11), X5.D-
VMD: C1.+, C2.+, R8.2, R10.1, R15.2, R18.1, VT2.3 (S), VT3.3 (S), VT6.3 (S), VT7.3 (S), X1.1
VREF: DD2.5 (VREF)
VREG5: C3.+, C14.1, DA1.2 (OUT), JP3.1
VREG33: C4.+, C13.1, DA2.2 (OUT), JP4.1
VS0: JP7.3, X17.1, X17.2, X17.3, X17.4, X17.5, X17.6, X17.7, X17.8, X17.9, X17.10, X25.1
VS1: DA1.3 (IN), DA2.3 (IN), JP6.3, X18.1, X18.2, X18.3, X18.4, X18.5, X18.6, X18.7, X18.8, X18.9, X18.10, X26.1

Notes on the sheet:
Servo 0-9
Servo 10-19
GPIO 0-7
AGPIO 0-7

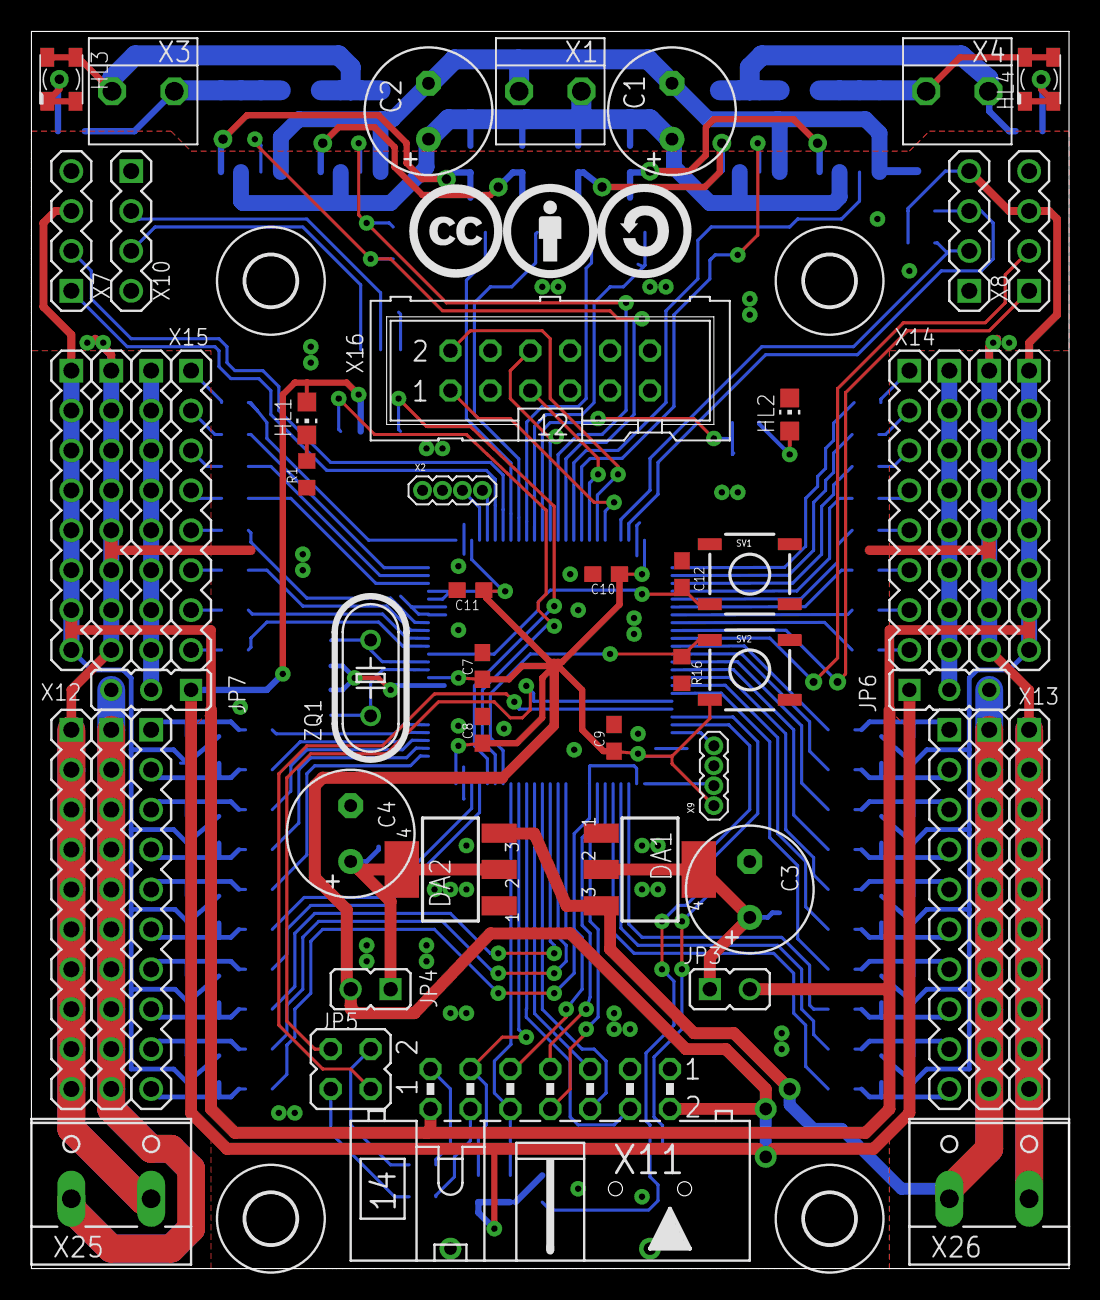
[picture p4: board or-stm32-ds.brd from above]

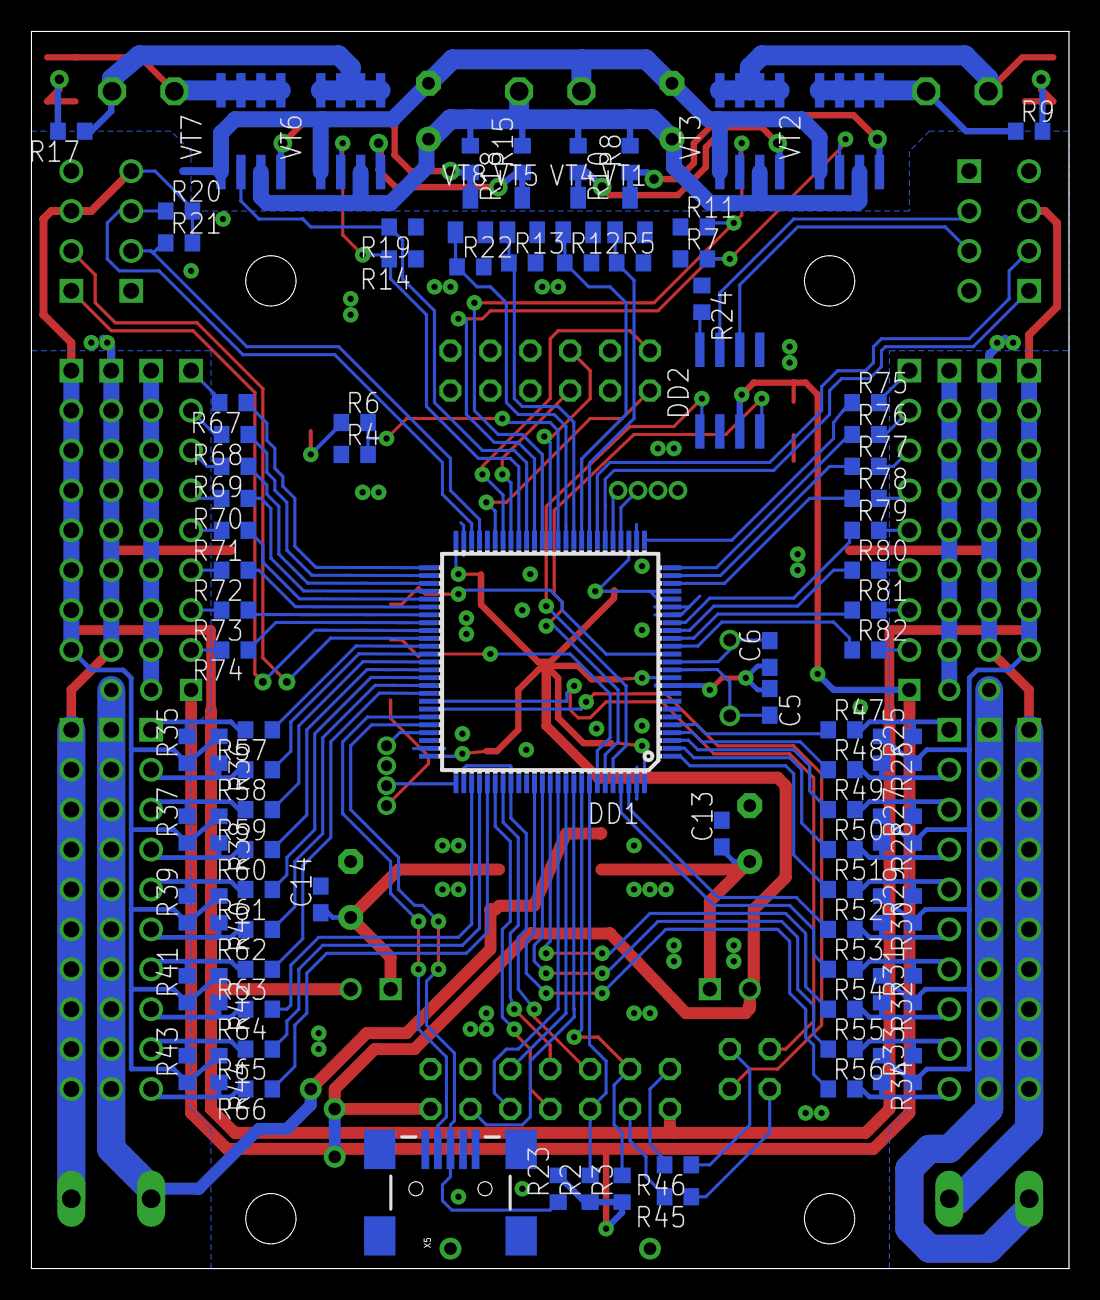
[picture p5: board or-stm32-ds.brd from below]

Board: 2 copper layers, 66.0 x 78.7 mm, 155 parts (95 on the bottom side), 142 nets.

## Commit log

2011-07-02 initial. import robobus & stm32f103 library
2011-07-03 lower case
    --HG--
    rename : RoboBus.lbr => robobus.lbr
2011-07-19 initial add sch
    [or-stm32-ds.sch]
2011-07-20 add frame
    [or-stm32-ds.sch]
2011-07-20 add servo connectors
    [or-stm32-ds.sch]
2011-07-20 add servo resistors
    [or-stm32-ds.brd, or-stm32-ds.sch]
2011-07-23 add GPIO and AGPIO headers
    [or-stm32-ds.brd, or-stm32-ds.sch]
2011-07-23 first pinout placement
    [or-stm32-ds.brd, or-stm32-ds.sch]
2011-07-23 replace RoboMD2-10P to RoboMD2
    [or-stm32-ds.brd, or-stm32-ds.sch]
2011-07-23 add USB, encoders
    [or-stm32-ds.brd, or-stm32-ds.sch]
2011-07-23 add CAN lib
    [or-stm32-ds.brd, or-stm32-ds.sch]
2011-07-23 add CAN
    [or-stm32-ds.brd, or-stm32-ds.sch]
2011-07-23 change jumper pads
    [or-stm32-ds.brd, or-stm32-ds.sch]
2011-07-23 move gpio
    [or-stm32-ds.brd, or-stm32-ds.sch]
2011-07-28 move connectors; reconnect servo pullup's
    [or-stm32-ds.brd, or-stm32-ds.sch]
2011-07-30 add LED2 lib
2011-07-30 led2.lbr: fixup name and pads
2011-07-30 add MD. Not completed
    [or-stm32-ds.brd, or-stm32-ds.sch]
2011-07-30 MD switch to 4-wire mode. Remove unneded logic
    [or-stm32-ds.brd, or-stm32-ds.sch]
2011-07-30 renumber sch
    [or-stm32-ds.brd, or-stm32-ds.sch]
2011-07-30 connect USB, CAN, ext I2C
    [or-stm32-ds.brd, or-stm32-ds.sch]
2011-07-30 connect TIM1
    [or-stm32-ds.brd, or-stm32-ds.sch]
2011-07-31 add rezonit.ru dru; better place for servo pull-up's (thanks =DeaD=); connect AGPIO
    [or-stm32-ds.brd, or-stm32-ds.sch]
2011-07-31 connect I2C, SPI, UART of RoboBus
    [or-stm32-ds.brd, or-stm32-ds.sch]
2011-07-31 connect GPIO; almost connected servo
    [or-stm32-ds.brd, or-stm32-ds.sch]
2011-07-31 connect 2-nd pad on MOSFEET's
    [or-stm32-ds.brd, or-stm32-ds.sch]
2011-08-06 Connect all servo; Add power supply; License CC-BY-SA
    [or-stm32-ds.brd, or-stm32-ds.sch]
2011-08-06 route servo, gpio, agpio, md2
    [or-stm32-ds.brd, or-stm32-ds.sch]
2011-08-06 route all servo, power supply
    [or-stm32-ds.brd, or-stm32-ds.sch]
2011-08-06 first route sprint done
    [or-stm32-ds.brd]
2011-08-06 Add gerber.cam; Add silk markers
    [or-stm32-ds.brd, or-stm32-ds.sch]
2011-08-06 FIX: wrong polarity on servo supply!
    [or-stm32-ds.brd]
2011-08-13 Add PCB4U dru
2011-08-13 Board complete. Rev. 0
    [or-stm32-ds.brd, or-stm32-ds.sch]
2011-08-13 Relese Rev. 0
    rename : devmapping.txt => doc/devmapping.txt
    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
    [or-stm32-ds.Drill.xln]
2011-11-01 Fix bugs, release Rev.1
    [or-stm32-ds.brd, or-stm32-ds.sch]
2011-11-01 gerber files for rev.1
    [or-stm32-ds.Drill.xln]
2012-07-19 Convert to Eagle 6 XML format
    [or-stm32-ds.brd, or-stm32-ds.sch]
